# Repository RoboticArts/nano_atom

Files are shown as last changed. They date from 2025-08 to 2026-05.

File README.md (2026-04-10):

  

# Meet Nano Atom!

<p align="center">
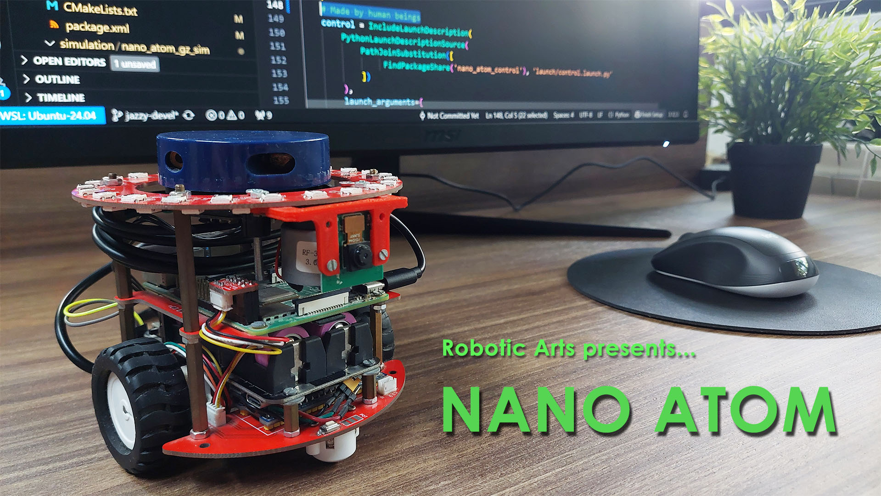
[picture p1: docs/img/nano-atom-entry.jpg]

</p>

## 1. Overview

### 1.1 Introduction

Nano Atom is an open-source mobile robot designed to emulate professional ROS robots at desktop scale, helping educators prepare students for future careers in robotics.

<p align="center">
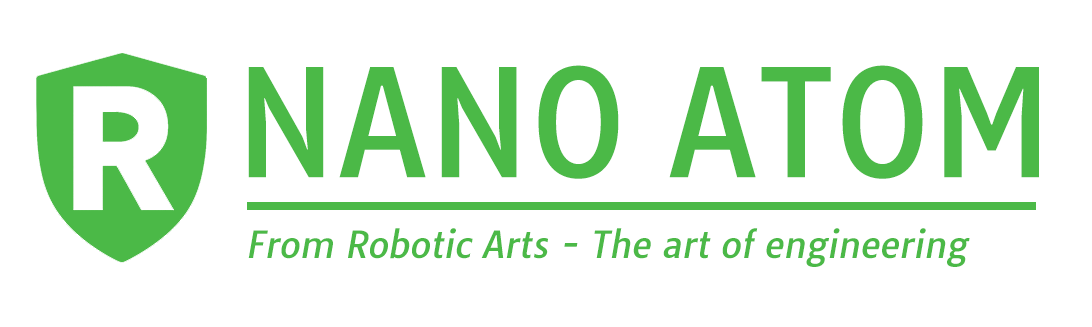
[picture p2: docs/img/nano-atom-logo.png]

</p>

Its mission is to make robotics more accessible to students, makers, and enthusiasts by offering a robot that is:

- **Affordable and accessible**, so more people can own a physical robot instead of relying only on simulation.
- **Professional-grade in miniature**, with sensors and architecture similar to commercial robots, but adapted to a desktop format.
- **Open source and modular**, allowing anyone to study its design, replicate it, modify it, and adapt it to their own interests.
- **Focused on hands-on learning**, clearly showing how hardware, software, control, simulation, and deployment come together in a real robotics project.

### 1.2 Specifications

Nano Atom packs the essential features of a ROS robot into a compact and affordable desktop format. The following specifications summarize its hardware and software capabilities.

- **Dimensions:** 11.5 × 11.5 × 11.5 cm  
- **Weight:** 350 g  
- **Onboard Computer:** Raspberry Pi 4 (4 GB RAM)  
- **LiDAR:** YDLIDAR X2 (360°, 8 m range)  
- **Camera:** OV5647 (5 MP, 1080p @ 30 fps)  
- **IMU:** Bosch BNO055 (9-axis sensor fusion)  
- **Wheel Encoders:** Quadrature Hall effect  
- **Maximum Speed:** 0.17 m/s  
- **Battery Life:** 2.5 – 4 h (≈2.5 h recharge time)  
- **Connectivity:** Wi-Fi, USB 3.0/2.0, GPIO  
- **Power Supply:** 5 V, 5000 mAh (regulated output)
- **Software:** ROS 2

### 1.3 Electronic System

See `hardware/electronics` for BOM and schematics.

<p align="center">
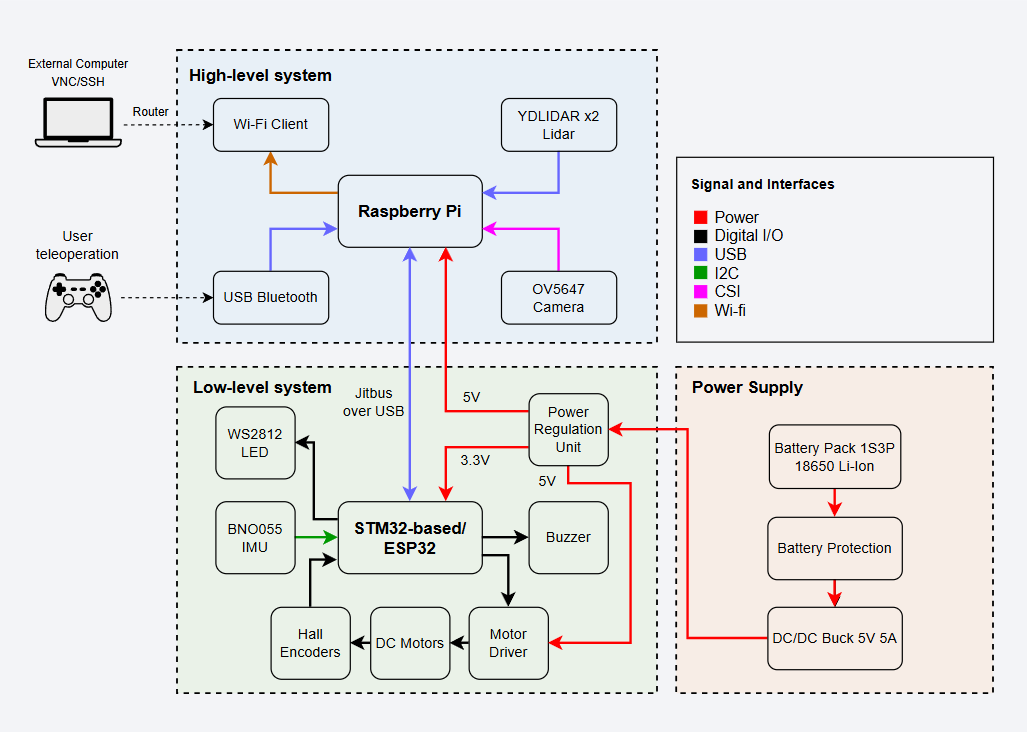
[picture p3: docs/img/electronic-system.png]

</p>

## 2. Quick start

*Requirements: Linux/WSL2, Docker v2.x and X11*

<p align="center">
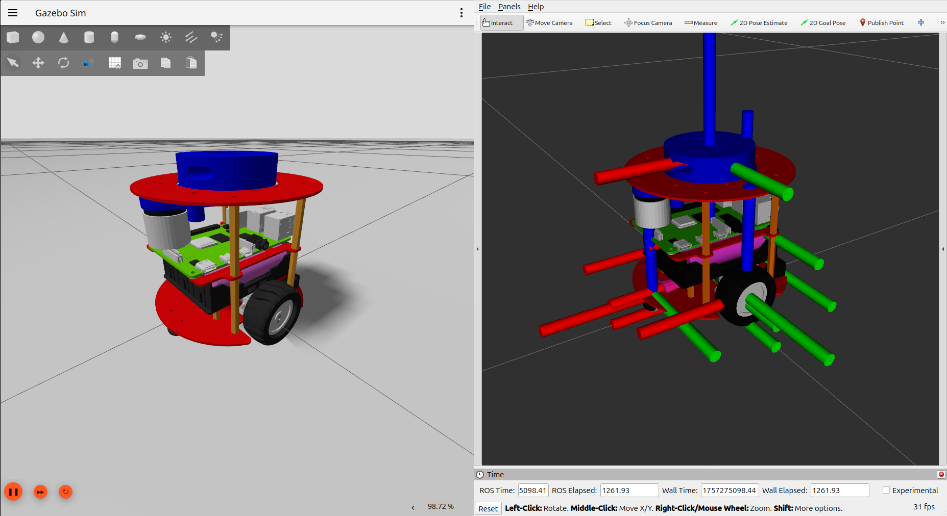
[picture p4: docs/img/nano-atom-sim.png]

</p>

### 2.1 Run Nano Atom

Get the docker compose file:

```
wget https://raw.githubusercontent.com/RoboticArts/nano_atom/refs/heads/jazzy-devel/docker/docker-compose.yaml
```

Enable GUI access for Docker:

```
xhost +local:root
```
**Note**: `xhost` temporarily enables GUI access in the current X11 session (Linux). You can revoke it anytime with `xhost -local:root`. Users on WSL2 can ignore it.

Run simulation:
```
docker compose up --pull always
```

### 2.2 Control Nano Atom

Open a new terminal and run teleop node:

```
docker exec -it nano-atom bash -ic "ros2 run teleop_twist_keyboard teleop_twist_keyboard --ros-args --remap cmd_vel:=/robot/robot_base_controller/cmd_vel -p stamped:=true"
```

## 3. Installation

### 3.1. Setup

Create the workspace:

```
mkdir -p ~/ros2_ws/src && cd ~/ros2_ws/src
```

Clone the repository:

```
git clone --branch jazzy-devel https://github.com/RoboticArts/nano_atom.git
```

### Option 1. Build from ROS2

Install dependencies:

```
cd ~/ros2_ws
rosdep update && rosdep install --from-paths src --ignore-src -y -r --rosdistro jazzy
```

Build the repository:

```
colcon build --symlink-install
source install/setup.bash
```

### Option 2. Build from Docker

Install CycloneDDS:

```
sudo apt-get update && sudo apt-get install ros-jazzy-rmw-cyclonedds-cpp
```

Build the docker image:

```
cd ~/ros2_ws/src/nano_atom
docker compose -f docker/docker-compose.build.yaml build
```

<!-- docker build -t nano-atom:build -f docker/Dockerfile . --> 

## 4. Bringup

### 4.1. Setup

Go to the repository root directory:

```
cd ~/ros2_ws/src/nano_atom
```

### Option 1. ROS2 launch

Run `nano_atom` packages:

```
ros2 launch nano_atom_base base.launch.py
```

### Option 2. Docker container

Run `nano atom` containers:

```
docker compose -f docker/docker-compose.build.yaml up
```

To access ROS 2 topics from your host, set CycloneDDS as the middleware:

```
export RMW_IMPLEMENTATION=rmw_cyclonedds_cpp
ros2 topic list
```

## 5. Development

### 5.1 Docker container

The `docker-compose.dev.yaml` uses `docker-compose.yaml` to load the host repository as a volume
and source the workspace. 

Go to the repository root directory:

```
cd ~/ros2_ws/src/nano_atom
```

Build docker (if needed):

```
docker compose -f docker/docker-compose.dev.yaml build
```

Start docker containers:

```
docker compose -f docker/docker-compose.dev.yaml up
```

Go inside the container:

```
docker exec -it nano-atom bash
```

## 6. Architecture

This section details the **planned** architecture of the `nano_atom` robot from the perspective of robotics development, acting as the backend for high-level applications.

<p align="center">
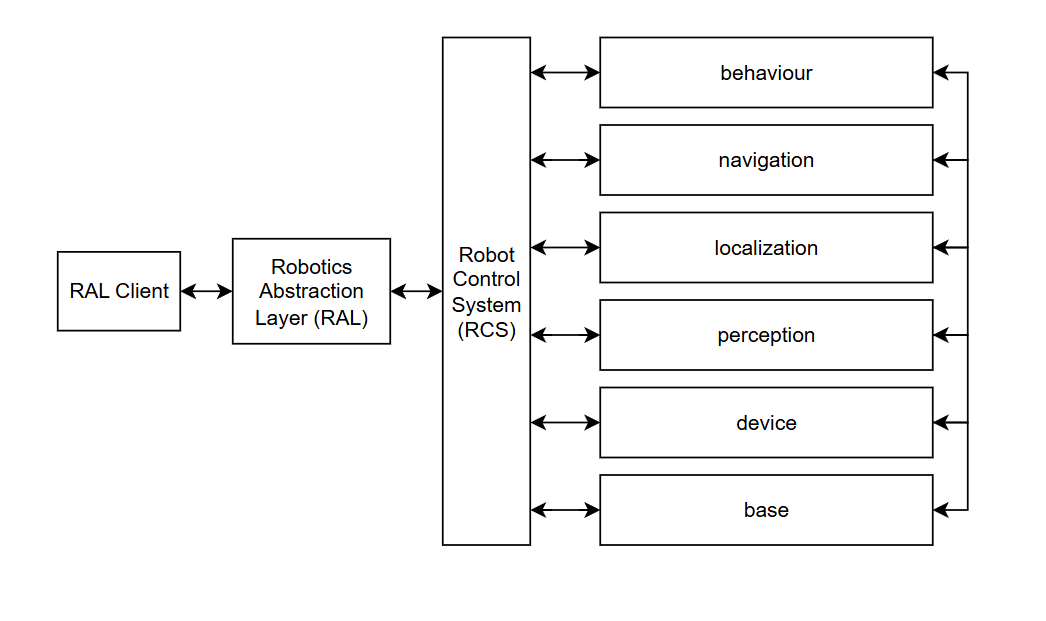
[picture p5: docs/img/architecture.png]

</p>

The software is arranged in different `modules`, each designed to accomplish a specific set of tasks. For example, localization focuses on guaranteeing the robot’s pose within an environment, while navigation provides a trajectory path.

The `modules` are based on a decoupled architecture, where communication between modules is allowed, but only through restrictive policies and standard interfaces. Together, they form the operative software (p.e. real time, control, etc), but they do not make decisions.

The `Robot Control System (RCS)` is responsible for decision-making, orchestrating and controlling each module. Its purpose is to translate high-level commands into concrete tasks for the modules.

The `Robotics Abstraction Layer (RAL)` provides a specification and a library that abstracts the logic of the `RCS` into standard commands using sockets. This ensures that user applications remain unchanged even if the internal logic evolves. 

The `RAL Client` provides access to the `RAL` interface in a specific programming language. With this design, developers do not need access to the library’s source code to execute commands on the robot, as all interactions are handled through the RAL Client via sockets.

## 7. CI Pipeline

The pipeline of this repository ensures that every commit triggers a clean build from scratch and runs the test suite to verify the changes. When a new version is tagged, the pipeline builds and publishes a Docker image to DockerHub.

The following diagram shows the CI architecture. For the technical implementation, see the `.github` and `scripts/ci` directories.

<p align="center">
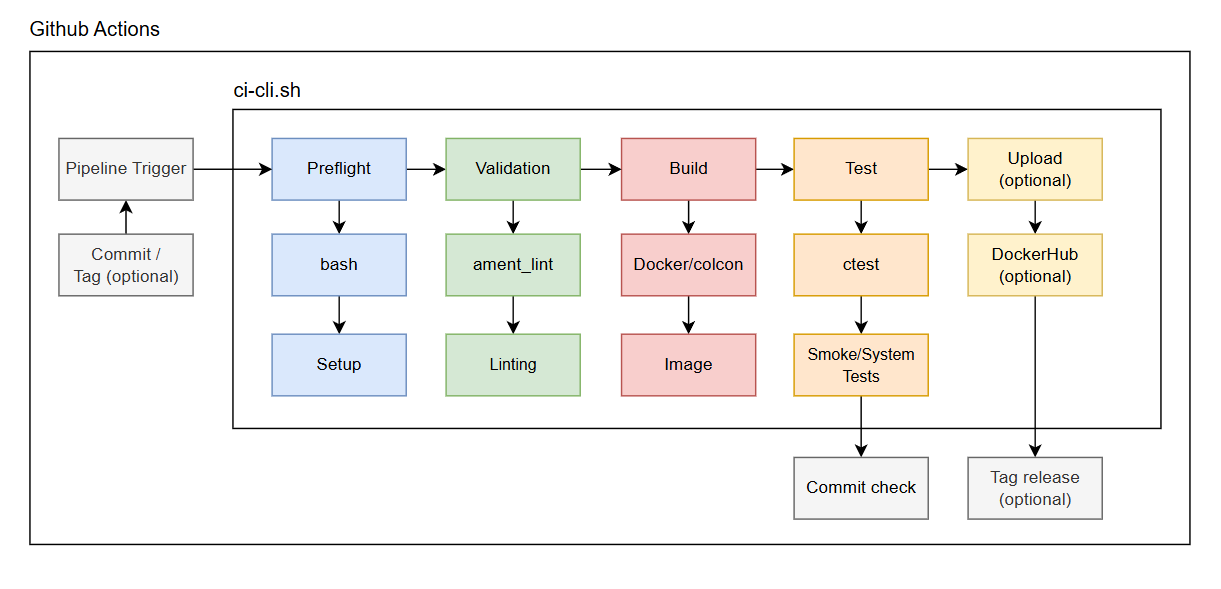
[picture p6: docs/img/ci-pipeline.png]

</p>

The CI pipeline is implemented using a GitHub Actions workflow, which orchestrates each stage through the `ci-cli` utility to manage the diferent pipeline phases.

Each step of the workflow calls `ci-cli --command <command>` to run these stages:

- **prefligh:** Ensures that files and directories are correctly structured before starting the CI process.
- **validation:** Runs static code analysis and linting checks.
- **build:** Uses a clean ROS Docker image to install and compile the ROS packages. The result is stored as a build artifact (Docker image).
- **test:** Executes the test suite on the generated artifact.
- **upload:** Pushes the Docker image to DockerHub, which serves as the staging area.

This architecture allows the `ci-cli` utility to be used seamlessly both locally and within the CI workflow. For example, running tests locally can be done with:

```
cd ~/ros2_ws/src/nano_atom
./scripts/ci/ci-cli.sh --command test
```

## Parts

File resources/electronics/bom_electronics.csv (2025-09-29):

ID | Name | Designator | Footprint | Quantity | Manufacturer Part | Manufacturer | Supplier | Supplier Part | Price
1 | GSC4417YA-16R4000 | BUZZER1 | BUZ-SMD_2P-L4.0-W4.0-L_GSC4317YA | 1 | GSC4417YA-16R4000 | INGHAi | LCSC | C255308 | 0.994
2 | 100nF | C1,C2,C5,C6,C8,C9 | C0805 | 6 | CC0805KRX7R9BB104 | YAGEO | LCSC | C49678 | 0.005
3 | 10uF | C3,C7 | CAP-SMD_L3.2-W2.8 | 2 | TAJB106K016RNJ | AVX | LCSC | C7193 | 0.186
4 | 22uF | C4 | CAP-SMD_L3.2-W1.6-R-RD | 1 | TAJA226K010RNJ | AVX | LCSC | C11366 | 0.195
5 | 100nF | CBST1 | C0805 | 1 | CC0805KRX7R8BB104 | YAGEO | LCSC | C519981 | 0.006
6 | 10uF | CIN1,CIN2 | C1206 | 2 | GRM31CR61E106KA12L | MuRata | LCSC | C77090 | 0.058
7 | 100nF | CINX1 | C0805 | 1 | GRM21BR71H104KA01L | MuRata | LCSC | C77082 | 0.01
8 | XH2.54-2AB | CN2 | CONN-SMD_2P-P2.54_XH2.54-2AB | 1
9 | 22uF | COUT1,COUT2 | C0805 | 2 | LMK212BJ226MG-T | TAIYO YUDEN | LCSC | C92814 | 0.032
10 | DSR1M_C908221 | D2 | SOD-123_L2.8-W1.8-LS3.7-RD | 1 | DSR1M | FUXINSEMI | LCSC | C908221 | 0.008
11 | MM3Z16_C123915 | D4 | SOD-323_L1.8-W1.3-LS2.5-RD | 1 | MM3Z16 | Shandong Jingdao Microelectronics | LCSC | C123915 | 0.014
12 | SL1210500 | F1 | F1210 | 1 | SL1210500 | TECHFUSE | LCSC | C70188 | 0.117
13 | ESP32 UART | H5 | CONN-TH_4P-P2.54_22232041 | 1 | 22232041 | MOLEX | LCSC | C164168 | 0.168
14 | BNO055 | IMU1 | BNO055 | 1 | BNO055
15 | 3.3uH | L3 | IND-SMD_L12.0-W12.0 | 1 | YPRH1204-3R3M | YJYCOIN | LCSC | C718280 | 0.287
16 | WS2812B-2020 | LED1,LED2,LED3,LED4 | LED-SMD_4P-L2.0-W2.0-TL_WS2812B-2020 | 4 | WS2812B-2020 | Worldsemi | LCSC | C965555 | 0.083
17 | FC-2012HRK-620D | LED5,LED6,LED7,LED8,LED9 | LED0805-RD | 5 | FC-2012HRK-620D | NATIONSTAR | LCSC | C84256 | 0.014
18 | POLOLU MOTOR | ML,MR | MOTOR POLOLU | 2
19 | Encoder Right Motor | P1 | CONN-SMD_6P-V-P1.50-R_X1502WVS-06-9TSN | 1 | X1502WVS-06-9TSN | XKB Enterprise | LCSC | C406145 | 0.149
20 | Encoder Left Motor | P2 | CONN-SMD_6P-V-P1.50-R_X1502WVS-06-9TSN | 1 | X1502WVS-06-9TSN | XKB Enterprise | LCSC | C406145 | 0.149
21 | Raspbery Pi | P3 | CONN-SMD_4P-V-P1.50-TR_X1502WVS | 1 | X1502WVS-04-9TSN | XKB Enterprise | LCSC | C406143 | 0.133
22 | 2n3904S | Q5 | SOT-23-3_L2.9-W1.3-P1.90-LS2.4-TR | 1 | 2n3904S-RTK/PS | KEC | LCSC | C18536 | 0.011
23 | 1K | R1,R2,R3,R4,R5,R6,R7,R9,R17,R22,R23 | R0805 | 11 | 0805W8F1001T5E | UniOhm | LCSC | C17513 | 0.002
24 | 10K | RFBB1 | R0805 | 1 | 0805W8F1002T5E | UniOhm | LCSC | C17414 | 0.002
25 | 54.9K | RFBT1 | R0805 | 1 | 0805W8F5492T5E | UniOhm | LCSC | C17747 | 0.002
26 | GT-TC029B-H025-L1N | SW2,SW3 | SW-SMD_L3.9-W2.9-P4.15-LS5.0 | 2 | GT-TC029B-H025-L1N | G-Switch | LCSC | C843669 | 0.082
27 | ESP32-WROOM-32 | U1 | WIFIM-SMD_ESP-32S | 1 | ESP32-WROOM-32 | Espressif Systems | LCSC | C82899 | 4.327
28 | SN74LVC1G139DCTR | U2 | SSOP-8_L2.9-W2.8-P0.65-LS4.0-BL | 1
29 | TB6612FNG,C,8,EL | U3 | SSOP-24_L8.3-W5.6-P0.65-LS7.6-BL | 1 | TB6612FNG,C,8,EL | TOSHIBA | LCSC | C141517 | 1.125
30 | AMS1117-3.3 | U4 | SOT-223-3_L6.7-W3.7-P2.30-LS7.0-BR | 1 | AMS1117-3.3 | JSMSEMI | LCSC | C917183 | 0.039
31 | TPS565201DDCR | U5 | TSOT-23-6_L2.9-W1.6-P0.95-LS2.8-BL | 1 | TPS565201DDCR | TI(德州仪器) | LCSC | C327676 | 0.143

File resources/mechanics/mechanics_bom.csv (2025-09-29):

Name | Units | Link | Total Unit | Total
Motor with encoders 155 rpm | 2 | https://www.robotshop.com | 12.2396 | 24.5872
Pair of rubber wheels 40 mm | 1 | https://www.robotshop.com | 6.5461 | 6.5461
DFRobot wheel caster | 2 | https://www.robotshop.com | 1.815 | 3.63
Wheel support pair | 1 | https://www.robotshop.com | 5.1183 | 5.1183
Battery 18650 Samsung 35E | 3 | https://www.androgeek.com | 4.9852 | 14.9556
Raspberry Pi 4 2GB | 1 | https://www.tiendatec.com | 40.9464 | 40.9464
SD Card SanDisk 32GB Class 10 | 1 | https://www.tiendatec.com | 7.139 | 7.139
Raspberry Pi Camera v1.3 | 1 | https://www.tiendatec.com | 9.9462 | 9.9462
YDLidar X2L | 1 | https://www.robotshop.com | 70.7608 | 70.7608

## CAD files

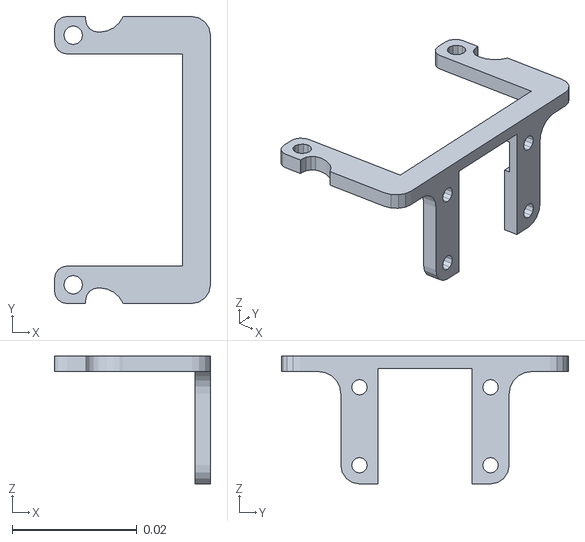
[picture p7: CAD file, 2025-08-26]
modules/base/nano_atom_description/meshes/accessories/ov5647_support.stl
0.025 x 0.046 x 0.0205

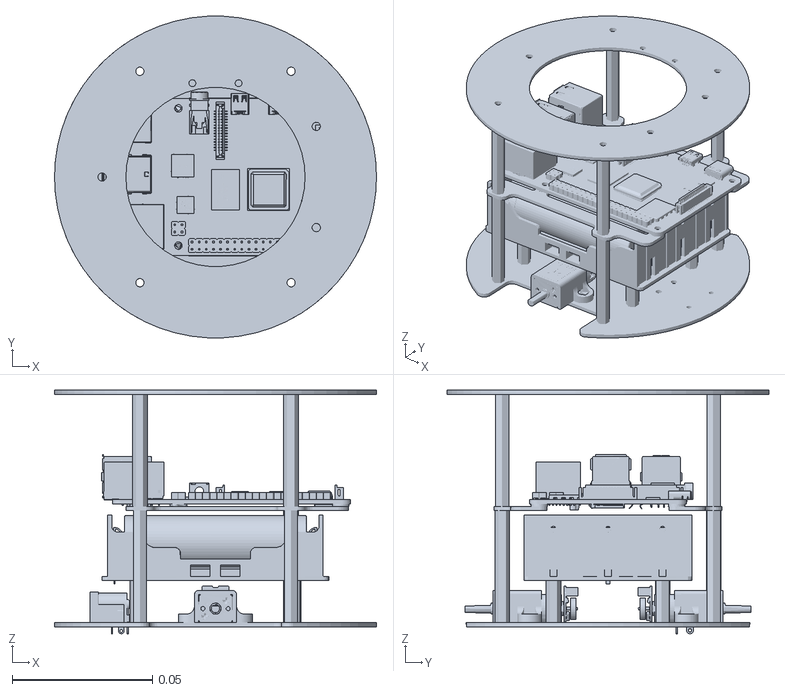
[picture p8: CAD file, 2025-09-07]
modules/base/nano_atom_description/meshes/bases/nano_atom_chassis.stl
0.115 x 0.115 x 0.087

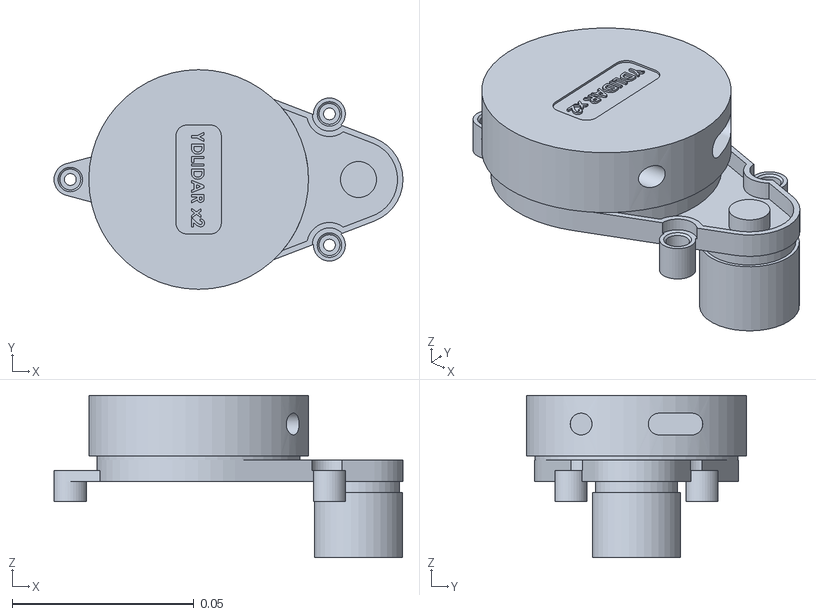
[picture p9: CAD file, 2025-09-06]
modules/base/nano_atom_description/meshes/devices/ydlidar_x2.stl
0.0961 x 0.0605 x 0.0447

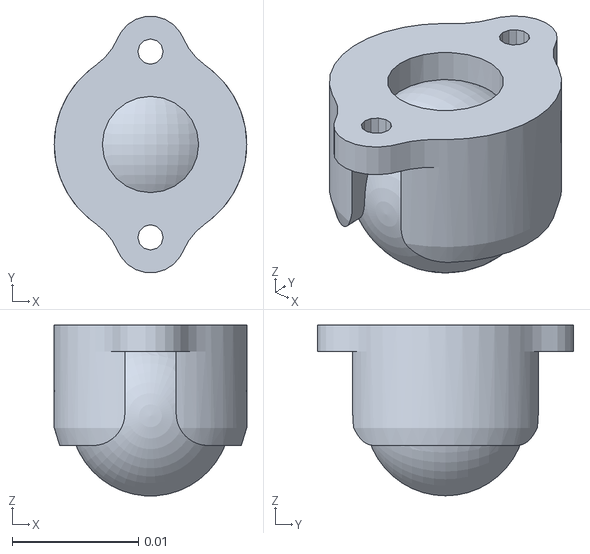
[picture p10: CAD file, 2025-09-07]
modules/base/nano_atom_description/meshes/wheels/nano_atom_caster_wheel.stl
0.0152 x 0.0203 x 0.0135

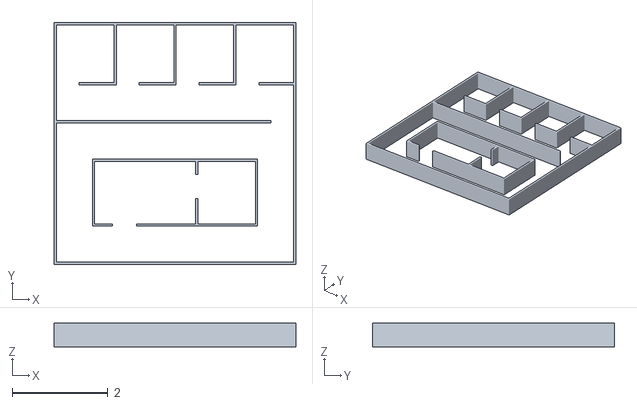
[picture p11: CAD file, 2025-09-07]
modules/simulation/nano_atom_gz_sim/models/nano_atom_office_walls/meshes/nano_atom_office_walls.STL
5.05 x 5.05 x 0.5

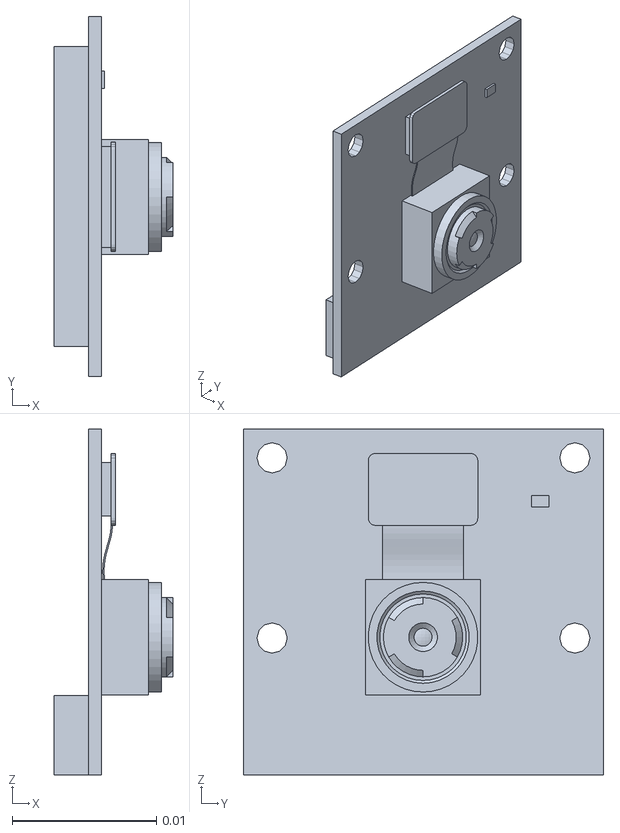
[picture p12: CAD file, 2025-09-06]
modules/base/nano_atom_description/meshes/devices/ov5647.stl
0.00825 x 0.025 x 0.024

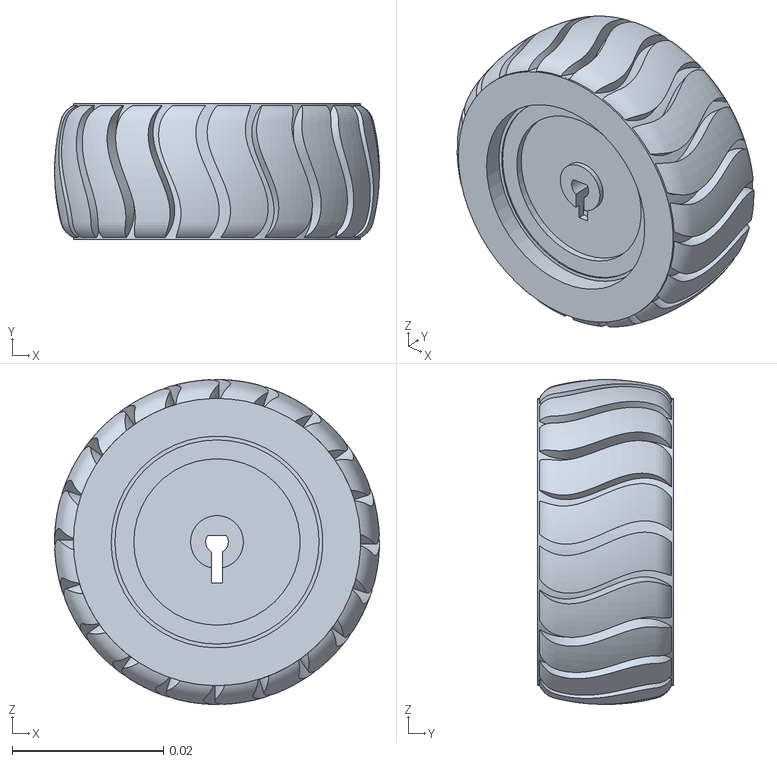
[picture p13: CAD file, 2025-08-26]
modules/base/nano_atom_description/meshes/wheels/nano_atom_right_rubber_wheel.stl
0.043 x 0.018 x 0.043

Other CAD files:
modules/base/nano_atom_description/meshes/wheels/nano_atom_left_rubber_wheel.stl

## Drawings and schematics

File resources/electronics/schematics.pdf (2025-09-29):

## UART1 Communication - MCU

## Battery Estimation - Power

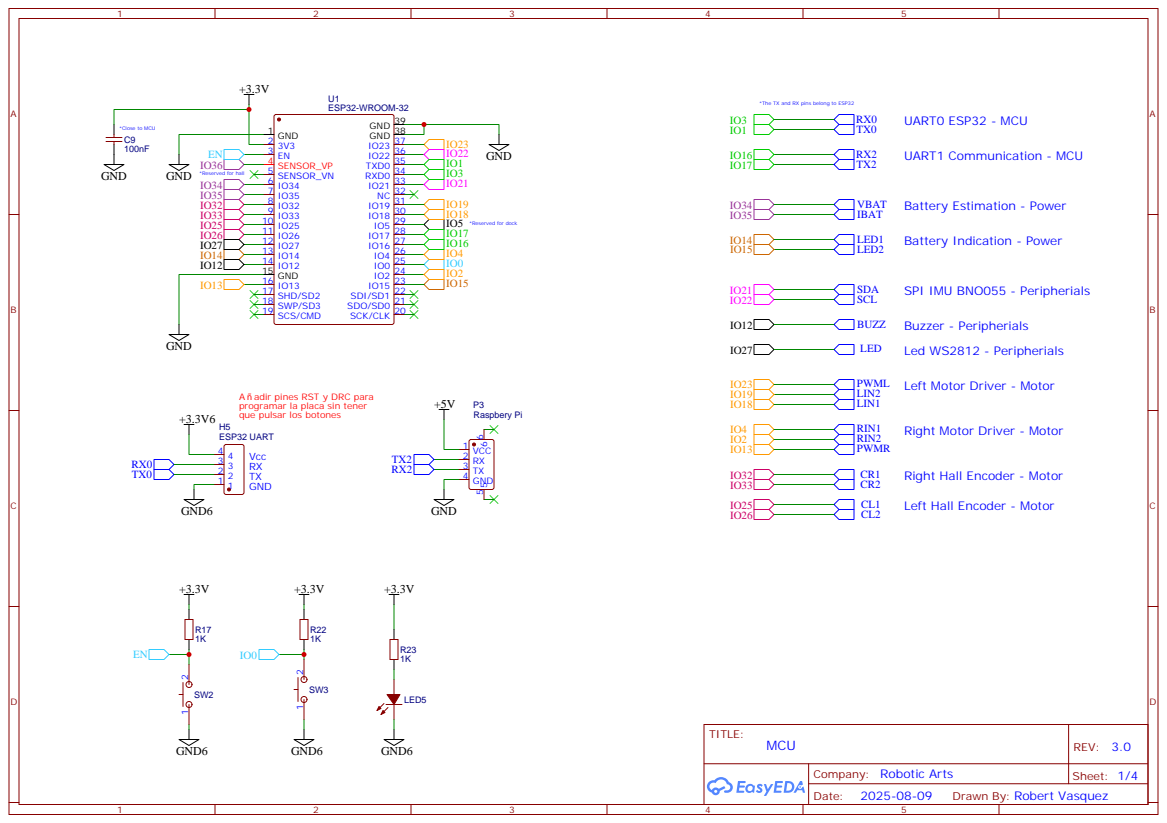
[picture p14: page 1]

*The TX and RX pins belong to ESP32

Left Motor Driver - Motor

Right Motor Driver - Motor

Right Hall Encoder - Motor

Left Hall Encoder - Motor

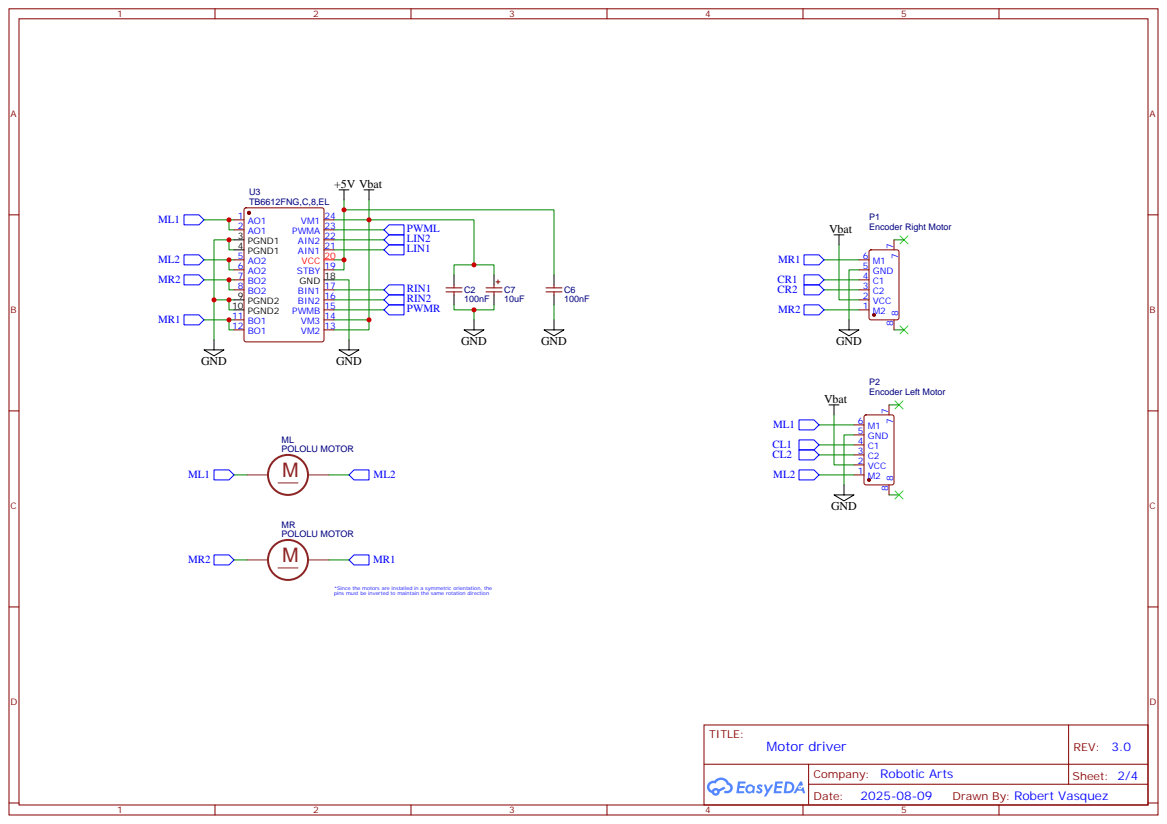
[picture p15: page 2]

*Since the motors are installed in a symmetric orientation, the
pins must be inverted to maintain the same rotation direction

## Dise ar schottky 5A low drop voltage

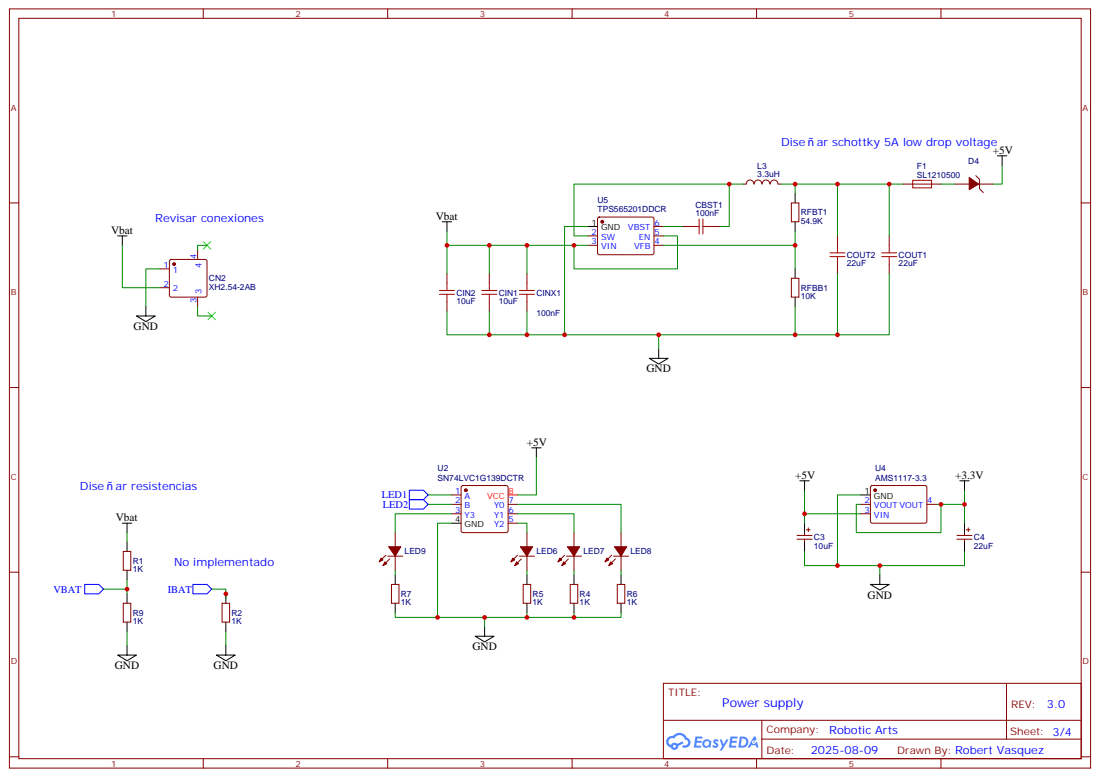
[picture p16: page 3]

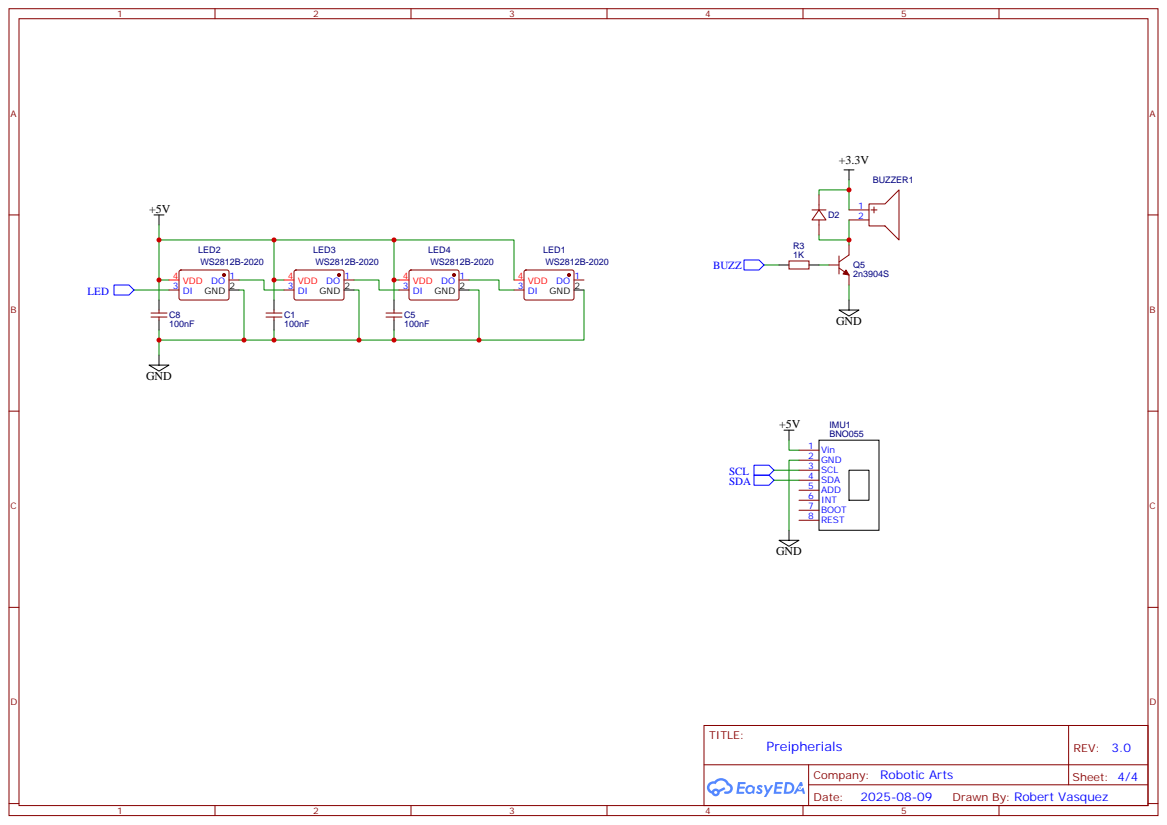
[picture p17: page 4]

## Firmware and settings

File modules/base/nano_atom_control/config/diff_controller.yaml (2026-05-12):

---
/**:
  controller_manager:
    ros__parameters:
      update_rate: 50  # Hz

      joint_state_broadcaster:
        type: joint_state_broadcaster/JointStateBroadcaster

      robot_base_controller:
        type: diff_drive_controller/DiffDriveController


  joint_state_broadcaster:
    ros__parameters:
      use_local_topics: false

  robot_base_controller:
    ros__parameters:

      # Joint names are local to the URDF/controller instance and are not affected by ROS namespaces
      left_wheel_names: ["left_wheel_joint"]
      right_wheel_names: ["right_wheel_joint"]

      wheel_separation: 0.0898
      wheel_radius: 0.021

      wheel_separation_multiplier: 1.18
      left_wheel_radius_multiplier: 1.0
      right_wheel_radius_multiplier: 1.0

      publish_rate: 50.0
      # TF prefixes are handled by controller_manager or gz_ros2_control namespace
      odom_frame_id: odom
      base_frame_id: base_footprint
      pose_covariance_diagonal : [0.001, 0.001, 0.001, 0.001, 0.001, 0.01]
      twist_covariance_diagonal: [0.001, 0.001, 0.001, 0.001, 0.001, 0.01]

      open_loop: false
      enable_odom_tf: true

      cmd_vel_timeout: 0.25
      #publish_limited_velocity: true
      #velocity_rolling_window_size: 10

      # Velocity and acceleration limits
      # Whenever a min_* is unspecified, default to -max_*
      linear.x.has_velocity_limits: true
      linear.x.max_velocity: 0.17
      linear.x.min_velocity: -0.17
      linear.x.has_acceleration_limits: true
      linear.x.max_acceleration: 12.0
      linear.x.min_acceleration: -12.0
      linear.x.has_jerk_limits: false
      linear.x.max_jerk: 0.0
      linear.x.min_jerk: 0.0

      angular.z.has_velocity_limits: true
      angular.z.max_velocity: 3.4
      angular.z.min_velocity: -3.4
      angular.z.has_acceleration_limits: true
      angular.z.max_acceleration: 12.0
      angular.z.min_acceleration: -12.0
      angular.z.has_jerk_limits: false
      angular.z.max_jerk: 0.0
      angular.z.min_jerk: 0.0

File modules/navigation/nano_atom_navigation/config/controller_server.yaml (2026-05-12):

/**:
  controller_server:
    ros__parameters:
      enable_stamped_cmd_vel: True
      controller_frequency: 10.0
      costmap_update_timeout: 0.30
      min_x_velocity_threshold: 0.001
      min_y_velocity_threshold: 0.001
      min_theta_velocity_threshold: 0.001
      failure_tolerance: 0.3
      progress_checker_plugins: ["progress_checker"]
      goal_checker_plugins: ["general_goal_checker"]
      controller_plugins: ["FollowPath"]
      use_realtime_priority: false

      # Progress checker
      progress_checker:
        plugin: "nav2_controller::SimpleProgressChecker"
        required_movement_radius: 0.02
        movement_time_allowance: 10.0

      # Goal checker
      general_goal_checker:
        stateful: True
        plugin: "nav2_controller::SimpleGoalChecker"
        xy_goal_tolerance: 0.05
        yaw_goal_tolerance: 0.05

      FollowPath:
        plugin: "nav2_regulated_pure_pursuit_controller::RegulatedPurePursuitController"
        desired_linear_vel: 0.1
        lookahead_dist: 0.3
        min_lookahead_dist: 0.6
        max_lookahead_dist: 0.9
        lookahead_time: 1.5
        rotate_to_heading_angular_vel: 1.0 # If rotate_to_heading is used, it is used as angular velocity
        transform_tolerance: 0.1
        use_velocity_scaled_lookahead_dist: false
        min_approach_linear_velocity: 0.05
        approach_velocity_scaling_dist: 0.6
        use_collision_detection: true
        max_allowed_time_to_collision_up_to_carrot: 5.0 # Limits the lookahead to the distance to the carrot
        use_regulated_linear_velocity_scaling: true
        use_fixed_curvature_lookahead: true
        curvature_lookahead_dist: 0.25
        use_cost_regulated_linear_velocity_scaling: false
        cost_scaling_dist: 0.3
        cost_scaling_gain: 1.0
        regulated_linear_scaling_min_radius: 0.9
        regulated_linear_scaling_min_speed: 0.25
        use_rotate_to_heading: true
        allow_reversing: false
        rotate_to_heading_min_angle: 0.785
        max_angular_accel: 3.2
        max_robot_pose_search_dist: 10.0
        min_distance_to_obstacle: 0.0
        stateful: true



  local_costmap:
    local_costmap:
      ros__parameters:
        update_frequency: 5.0
        publish_frequency: 2.0
        global_frame: $(var robot_prefix)odom
        robot_base_frame: $(var robot_prefix)base_link
        rolling_window: True
        width: 2
        height: 2
        resolution: 0.02
        robot_radius: 0.075 # Footprint
        plugins: ["obstacle_layer", "inflation_layer"]
        obstacle_layer:
          plugin: "nav2_costmap_2d::ObstacleLayer"
          enabled: True
          observation_sources: front_laser
          front_laser:
            topic: front_laser/scan
            max_obstacle_height: 2.0
            clearing: True
            marking: True
            data_type: "LaserScan"
            raytrace_max_range: 3.0
            raytrace_min_range: 0.0
            obstacle_max_range: 2.5
            obstacle_min_range: 0.0
        inflation_layer:
          plugin: "nav2_costmap_2d::InflationLayer"
          cost_scaling_factor: 10.0
          inflation_radius: 0.15
        always_send_full_costmap: True

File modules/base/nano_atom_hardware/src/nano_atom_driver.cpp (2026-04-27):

// Copyright (C) 2025, Robotic Arts
//
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
// Author: Robert Vasquez Zavaleta

#include "nano_atom_hardware/nano_atom_driver.hpp"

NanoAtomDriver::NanoAtomDriver(const std::string& serial_port, const int serial_baudrate,
                                const int serial_timeout, const int resolution)
{
  std::cout << "Configure serial" << std::endl;
  (void)resolution;

  jit_ = std::make_unique<SerialJitbus>();
  
  if (jit_->init(serial_port.c_str(), serial_baudrate, serial_timeout))
  { 
    std::cout << "Serial port opened! \n";
  }

  hardware_thread_ = std::jthread(
    [this](std::stop_token st){
      hardware_loop(st);
  });

}

void NanoAtomDriver::hardware_loop(std::stop_token st)
{
  while(!st.stop_requested())
  {
    if (jit_->available() > 0)
    {
      std::lock_guard<std::mutex> lock(jitbus_mutex_); 
      jit_->receivePacket(motor_state_, 1);
    }
    std::this_thread::sleep_for(std::chrono::milliseconds(1));
  }
}

void NanoAtomDriver::setWheelCommand(const DiffDriveCommand& command)
{
  motor_setpoint_[0] = static_cast<float>(command.left_wheel.velocity);
  motor_setpoint_[1] = static_cast<float>(command.right_wheel.velocity);

  jit_->sendPacket(motor_setpoint_, 2);
  
  //std::cout << "Set wheel commands! \n";
  //std::cout << "Left: " << motor_setpoint_[0] << "\n";
  //std::cout << "Right: " << motor_setpoint_[1] << "\n";
}

void NanoAtomDriver::getWheelState(DiffDriveState& state)
{
  std::lock_guard<std::mutex> lock(jitbus_mutex_);

  state.left_wheel.position = motor_state_.position[0];
  state.left_wheel.velocity = motor_state_.velocity[0];
  state.right_wheel.position = motor_state_.position[1];
  state.right_wheel.velocity = motor_state_.velocity[1];

  // std::cout << "Get wheel states! \n";
  // std::cout << "Left Wheel \n";
  // std::cout << " - Position: " << state.left_wheel.position << "\n";
  // std::cout << " - Velocity: " << state.left_wheel.velocity << "\n";
  // std::cout << "Right Wheel \n";
  // std::cout << " - Position: " << state.right_wheel.position << "\n";
  // std::cout << " - Velocity: " << state.right_wheel.velocity << "\n";
}

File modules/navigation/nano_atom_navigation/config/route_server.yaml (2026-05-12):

/**:
  route_server:
    ros__parameters:
      # The graph_filepath does not need to be specified since it going to be set by defaults in launch.
      # If you'd rather set it in the yaml, remove the default "graph" value in the launch file(s).
      # file & provide full path to map below. If graph config or launch default is provided, it is used
      # graph_filepath: $(find-pkg-share nav2_route)/graphs/aws_graph.geojson
      boundary_radius_to_achieve_node: 1.0
      radius_to_achieve_node: 0.1
      smooth_corners: true
      smoothing_radius: 0.2
      route_frame: map 
      base_frame: $(var robot_prefix)base_link
      operations: ["AdjustSpeedLimit", "ReroutingService", "CollisionMonitor"]
      ReroutingService:
        plugin: "nav2_route::ReroutingService"
      AdjustSpeedLimit:
        plugin: "nav2_route::AdjustSpeedLimit"
      CollisionMonitor:
        plugin: "nav2_route::CollisionMonitor"
        max_collision_dist: 3.0
      edge_cost_functions: ["DistanceScorer", "CostmapScorer"]
      DistanceScorer:
        plugin: "nav2_route::DistanceScorer"
      CostmapScorer:
        plugin: "nav2_route::CostmapScorer"
      prune_goal: true   

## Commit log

2025-08-26 nano_atom: Add simulation and hardware structure
    [caster_wheel.urdf.xacro, diff.ros2_control.urdf.xacro, diff_controller.yaml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]
2025-09-06 base: Add '/' instead of '_' for tf prefixes
    [diff_controller.yaml]
2025-09-06 base/nano_atom_description: Add basic sensors and colors
    [imu.urdf.xacro, nano_atom_base.urdf.xacro, nano_atom_std.urdf.xacro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]
2025-09-07 base/nano_atom_description: Update and improve meshes
    [caster_wheel.urdf.xacro, nano_atom_base.urdf.xacro, nano_atom_caster_wheel.stl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]
2025-09-07 nano_atom: Move base/nano_atom_simulation to simulation/nano_atom_gz_sim
    [model.sdf, nano_atom_office_walls.STL]
2025-09-20 base: Fix wheel separation and radius
    [diff_controller.yaml]
2025-09-20 base/description: Add ov5647 camera
    [nano_atom_std.urdf.xacro, ov5647.urdf.xacro, ov5647_support.urdf.xacro]
2025-09-20 base/description: Fix gazebo lidar scan
    [ydlidar_x2.urdf.xacro]
2025-09-20 simulation: Add camera bridge
2025-09-20 base/description: Add IMU noise
    [imu.urdf.xacro]
2025-09-29 nano_atom: Add hardware resources
    [bom_electronics.csv, mechanics_bom.csv]
2025-10-11 feat: Add localization and navigation (#3)
    [controller_server.yaml, diff_controller.yaml]
2026-04-27 feat: Add hardware interface (#4)
    * base: Add hardware interface structure
    * devices: Add ydlidar laser
    * base/hw: Implement nano atom driver for hardware interface
    * base: Add jitbus and roboticarts_pad submodules
    * base: Update roboticarts_pad for stamped cmd_vel
    * docker: Add libserial dependency in dockerfile
    [diff.ros2_control.urdf.xacro, diff_controller.yaml, hardware.yaml]
2026-05-11 refactor: Folder reanaming, startup and camera_ros for rpi (#5)
    [bom_electronics.csv, caster_wheel.urdf.xacro, controller_server.yaml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]
2026-05-12 feat: Add devices module (#6)
    - Add devices module including laser and camera sensors
    - Add teleoperation, twist mux and rviz configuration
    - Fix CI to work with modules folder and exclude camera_ros from license test
2026-05-12 feat: Add configurable launch parameters and startup orchestration (#7)
    [controller_server.yaml, diff.ros2_control.urdf.xacro, diff_controller.yaml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]

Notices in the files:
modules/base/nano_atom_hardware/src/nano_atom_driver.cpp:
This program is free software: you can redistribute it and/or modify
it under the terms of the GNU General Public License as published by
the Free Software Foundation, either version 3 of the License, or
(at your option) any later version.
